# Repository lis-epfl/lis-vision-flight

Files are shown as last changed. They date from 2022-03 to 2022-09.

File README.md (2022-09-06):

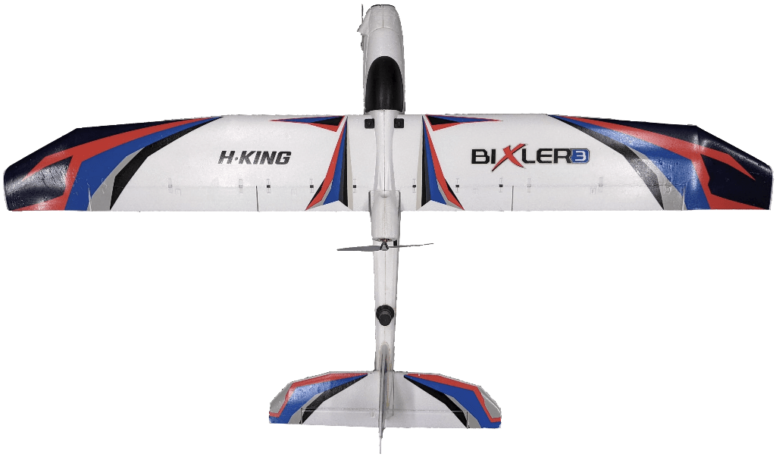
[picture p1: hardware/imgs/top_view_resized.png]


# LIS Vision Flight

Open source, simple fixed-wing drone for vision-based flight experiments

The LIS Vision flight project aims to give easy access to a vision-based fixed-wing drone to conduct experiments. It features

- a global shutter camera for vision-based applications
- an oboard single board computer to process vision data and for control
- a flow sensor and a point lidar for vision-based pose estimation
- a high precision RTK GNSS to provide ground truth data
- airspeed sensor for estimates of wind speeds
- a telemetry radio for communication with a ground station
- a PX4 autopilot that handles
  - sensor reading
  - actuator commanding
  - state estimation
  - time-synced camera triggering
  - attitude control
  - communication for RTK corrections

## Hardware

Instructions for building the drone can be found in [hardware](./hardware).

## Software

Find the instructions for the software setup in [software](./software).

## Citation

``` bibtex
@inproceedings{wueest2018accurate,
  title={Accurate Vision-based Flight with Fixed-Wing Drones},
  author={W{\"u}est, Valentin and Ajanic, Enrico and M{\"u}ller, Matthias and Floreano, Dario},
  booktitle={2022 IEEE/RSJ International Conference on Intelligent Robots and Systems (IROS)},
  year={2022},
  organization={IEEE}
}
```

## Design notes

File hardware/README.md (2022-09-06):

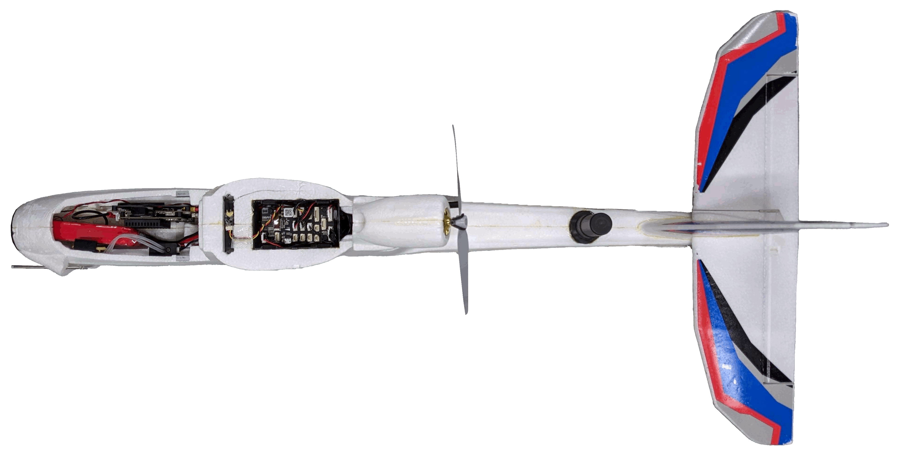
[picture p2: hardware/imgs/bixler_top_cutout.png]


# Hardware
## Parts list

We first provide a list of hardware components. The prices listed are based on online prices on March 11, 2022 and are listed in Euros.

### Body and actuation
| Part Function | Article Name | Amount | Price | Total Price |
| --- | --- | :----: | ----: | ---: |
| fixed-wing plane | H-King Bixler 3 Glider 1550mm (61") Kit | 1 | 100 | 100 |
| wing servos | Corona CS-929MG | 2 | 6 | 12 |
| elevator, rudder servo | Corona DS-919MG | 2 | 5 | 10 |
| thrust motor | Scorpion SII-2212-1400 KV (V2) | 1 | 42 | 42 |
| propeller | GWS EP-8040 | 1 | 5 | 5 |
| electronic speed controller (ESC) | Flycolor X-Cross Slim BL32 36A | 1 | 14 | 14 |
| battery | NVision LiPo 2400 mAh 3S 35C | 1 | 22 | 22 |
| power module | Micro Power Module (PM06 v2) | 1 | 15 | 15 |
| | | | | **220** |

### Autopilot 
| Part Function | Article Name | Amount | Price | Total Price |
| --- | --- | :----: | ----: | ---: |
| autopilot | Pixhawk 4 (plastic case) | 1 | 168 | 168 |
| RC receiver | FrSky R-XSR 2.4GHz 16CH ACCST | 1 | 21 | 21 |
| telemetry | Transceiver Telemetry Radio V3 500mW Telemetry Radio V3 433MHz | 1 | 51 | 51 |
| airspeed sensor | Sensirion SDP33 kit | 1 | 40 | 40 |
| GNSS antenna | Drotek DA233 | 1 | 70 | 70 |
| GNSS module | Drotek DP0601 | 1 | 170 | 170 |
| GNSS extension cable | 415-0031-MM250 | 1 | 15 | 15 |
| GNSS cable adapter | ADP-SMAM-SMAF90 | 1 | 6 | 6 |
| sd card autopilot | Sandisk Extreme microSDHC 16GB | 1 | 15 | 15 |
| | | | | **556** |

### Vision and companion computer
| Part Function | Article Name | Amount | Price | Total Price |
| --- | --- | :----: | ----: | ---: |
| camera | Flir Firefly S FFY-U3-16S2M-S | 1 | 190 | 190 |
| lens | Arducam 1/2.5" M12 6mm M2506ZH04 | 1 | 9 | 9 |
| single board computer (SBC) | Nvidia Jetson Nano | 1 | 121 | 121 |
| carrier board | Nvidia Jetson Nano Carrier Board | 1 | 100 | 100 |
| heatsink | ICK PGA 16 X 16 X 8 | 1 | 3 | 3 |
| usb wifi | TP-Link Archer T3U AC1300 Mini | 1 | 20 | 20 |
| sd card SBC | Sandisk Extreme microSDXC 64GB | 1 | 12 | 12 |
| | | | | **455** |

### Ground station

| Part Function  | Article Name | Amount | Price | Total Price |
| --- | --- | :----: | ----: | ---: |
| Laptop | - | 1 | - | - |
| Remote Control | FrSky Taranis X9D | 1 | 214 | 214 |
| Wifi Router | Ubiquity AmpliFi HD Mesh Router | 1 | 136 | 136 |
| Modem | Netgear LB2120 | 1 | 145 | 145 |
| GNSS antenna | Drotek DA233 | 1 | 70 | 70 |
| GNSS module | Drotek DP0601 | 1 | 170 | 170 |
| | | | | **735** |

### 3D printed parts
| Name | link | Image | Description |
| --- | --- | --- | --- |
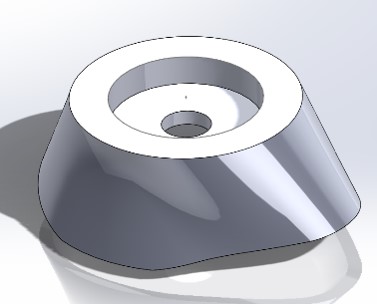
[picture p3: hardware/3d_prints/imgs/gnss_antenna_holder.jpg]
GNSS antenna holder
| GNSS antenna holder | [SLDPRT](3d_prints/gnss_antenna_holder.SLDPRT)<br />[STL](3d_prints/gnss_antenna_holder.STL)<br />[STEP](3d_prints/gnss_antenna_holder.STEP) |  | Attachment point for GNSS antenna. See step 2. |
| Pixhawk 4 foot (x2) | [SLDPRT](3d_prints/pixhawk_foot.SLDPRT)<br />[STL](3d_prints/pixhawk_foot.STL) | Pixhawk 4 foot | Tap M3 threads and attach to naked Pixhawk 4 board with nylon screws. See step 6 for instructions. |
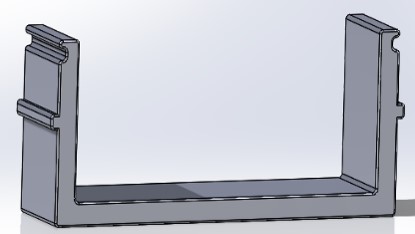
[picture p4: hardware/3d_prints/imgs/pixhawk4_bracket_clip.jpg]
Pixhawk 4 bracket clip
| Pixhawk 4 bracket clip (x2) | [SLDPRT](3d_prints/pixhawk_bracket_clip.SLDPRT)<br />[STL](3d_prints/pixhawk_bracket_clip.STL) |   | This part slides and clicks into place inside the "Pixhawk 4 bay". See step 6 for instructions. |
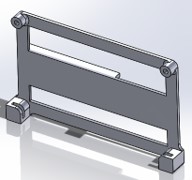
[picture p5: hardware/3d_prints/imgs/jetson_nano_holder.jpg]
Jetson nano holder
| Jetson nano holder | [SLDPRT](3d_prints/jetson_nano_holder.SLDPRT)<br />[STL](3d_prints/jetson_nano_holder.STL) |  | This part is glued with its back onto the right side of the front bay as shown in the picture of step 8. Two holes should be tapped with M3 thread to attach the LisNano board by its upper holes. Glue and test-fit the LisNano befor the assembly of the fuselage halves. |
| Airspeed sensor holder | [SLDPRT](3d_prints/airspeed_sensor_holder.SLDPRT)<br />[STL](3d_prints/airspeed_sensor_holder.STL) | Airspeed sensor holder | Tap M3 thread in the holes. Glue onto the shoulder on the left of the front bay as visible in the picture of step 8. |
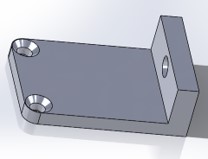
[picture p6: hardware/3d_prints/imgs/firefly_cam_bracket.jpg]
Firefly camera bracket
| Firefly camera bracket (x2) | [SLDPRT](3d_prints/firefly_camera_bracket.SLDPRT)<br />[STL](3d_prints/firefly_camera_bracket.STL) |  | Bracket to hold the Firefly camera in place. The two holes on the side allow screwing it onto the camera, the singular screw hole allow it to be inserted into the nose part and attached to it with an M3 nylon screw as shown in step 8. |
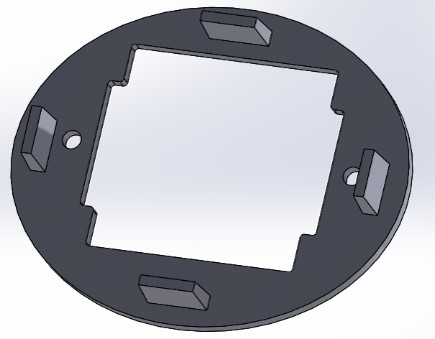
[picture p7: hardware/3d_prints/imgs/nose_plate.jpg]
Nose plate
| Nose plate | [SLDPRT](3d_prints/nose_plate.SLDPRT)<br />[STL](3d_prints/nose_plate.STL) |  | This part is glued to the front of the fuselage as visible in step 8. It accepts the front camera with brackets. Tap the holes with M3. |
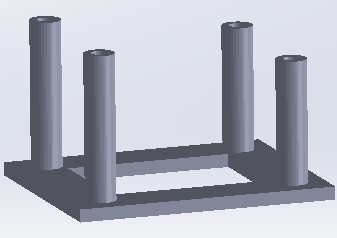
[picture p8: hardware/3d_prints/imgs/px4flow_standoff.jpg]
PX4Flow standoff
| PX4Flow standoff | [SLDPRT](3d_prints/px4flow_standoff.SLDPRT)<br />[STL](3d_prints/px4flow_standoff.STL) |  | This part is glued to the bottom inside the fuselage of the Bixler, see step 9. Make sure, the smaller standoffs are towards the back of the plane as they serve to level the flow sensor.  Tap M3 holes into the standoff. |
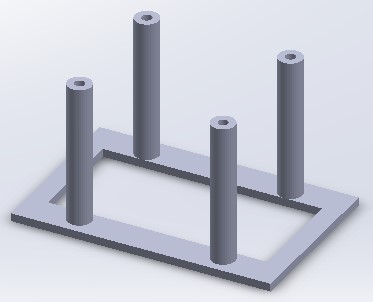
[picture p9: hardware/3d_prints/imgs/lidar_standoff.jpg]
PX4Flow standoff
| Lidar standoff | [SLDPRT](3d_prints/px4flow_standoff.SLDPRT)<br />[STL](3d_prints/lidar_standoff.STL) |  | The lidar standoff is placed inside the fuselage towards the front as shown in the figure in step 9. It is glued onto the fuselage with epoxy. Tap M3 holes into the standoff. |
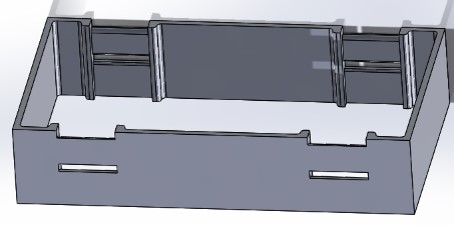
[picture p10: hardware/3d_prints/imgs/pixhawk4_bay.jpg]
Pixhawk 4 bay
| Pixhawk 4 bay | [SLDPRT](3d_prints/pixhawk_bay.SLDPRT)<br />[STL](3d_prints/pixhawk_bay.STL) |  | Is glued into the under-wing bay in step 10. The slot needs to be cut out slightly to fit. Make sure it's not deformed when inserted for glueing and that there is no epoxy in the slots and slits. |

### Tools

- M3 tap
- 5min epoxy
- servo tester

### Prepare body

We first give a short overview of most electornic parts that will be put inside the Bixler. Hopefully, this will serve as a guiding help.
*Note*: We use 5min epoxy to glue if not mentioned otherwise.

Bixler insides

**Step 1** Start printing all STL files which you find in the folder [3d_prints](3d_prints). Tap M3 threads into the 2 Pixhawk 4 feet, the Jetson nano holder, the airspeed sensor holder, the 2 Firefly camera brackets, the nose plate, the PX4Flow standoff and the lidar standoff.

**Step 2** Carve a groove into the tail of the Bixler to allow the antenna extension cable (SMA cable) to go from the tail to the fuselage as shown in the picture. Take the GNSS antenna holder and screw the male side of the SMA cable into it. This part (with SMA cable attached) is glued into the tail section of one of the fuselage parts (before fuselage halves are glued together). The SMA cable is glued into the groove cut in the fuselage half. The other end of the SMA cable should exit into the under-wing bay of the fuselage, high enough to allow screwing the GNSS module into the SMA connector, as shown in the picture.

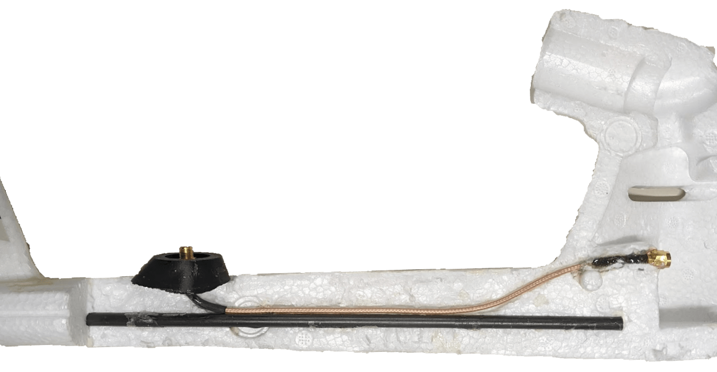
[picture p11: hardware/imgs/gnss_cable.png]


**Step 3** Set all servos to a zero position. You can do this with a servo tester or simply power it through the autopilot. Take the rudder/elevator-servos (2x Corona CS-929MG) and attach the arms at 90° angle such that they are facing outwards the fuselage. Connect the rods to the elevator and rudder in a hole in the servo arm at about 1.3cm distance and attach the arms to the servos. Now, glue the servos in place as shown in the picture.

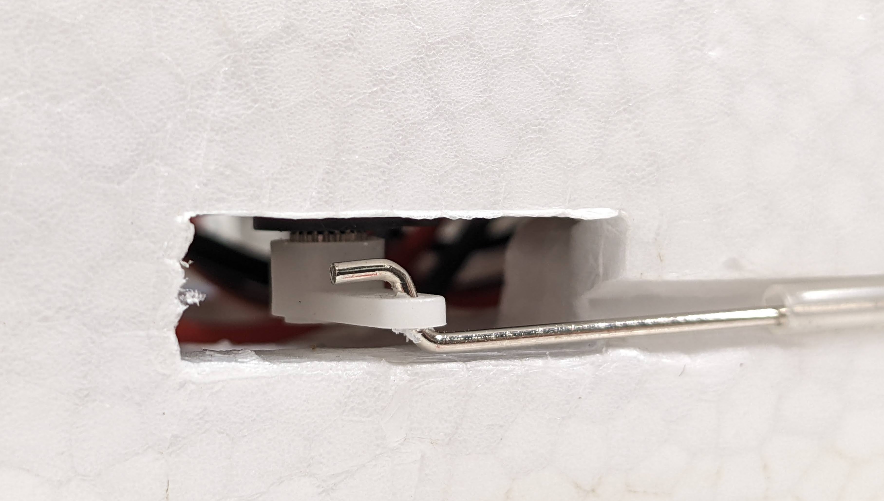
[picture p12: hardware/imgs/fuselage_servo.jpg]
outside
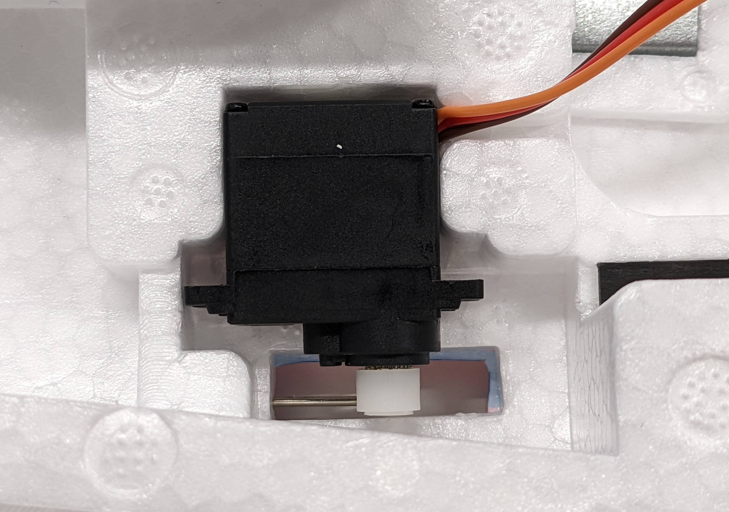
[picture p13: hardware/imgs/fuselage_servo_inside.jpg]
inside
    

**Step 4** Extend the wing servos cables. Then, attach the arms to the wing servos at a 90° angle and glue them in the wing. Attach the actuation rods as shown in the pic at a radius of about 1.1cm from the servo rotation center. For all actuation plastic parts, choose the second most outer hole. If you choose others, you will have to tune your controller accordingly afterwards. Then, glue in the plastic hinges on the ailerons and flaps. Finally, glue the flaps and the ailerons together by inserting a piece of foam as shown in the second picture and move ailerons and flaps to break them in.

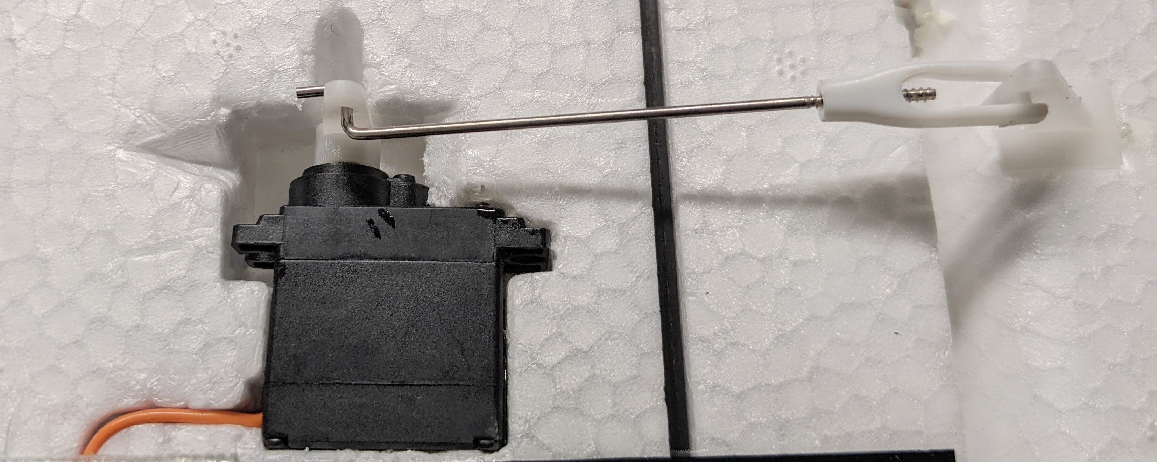
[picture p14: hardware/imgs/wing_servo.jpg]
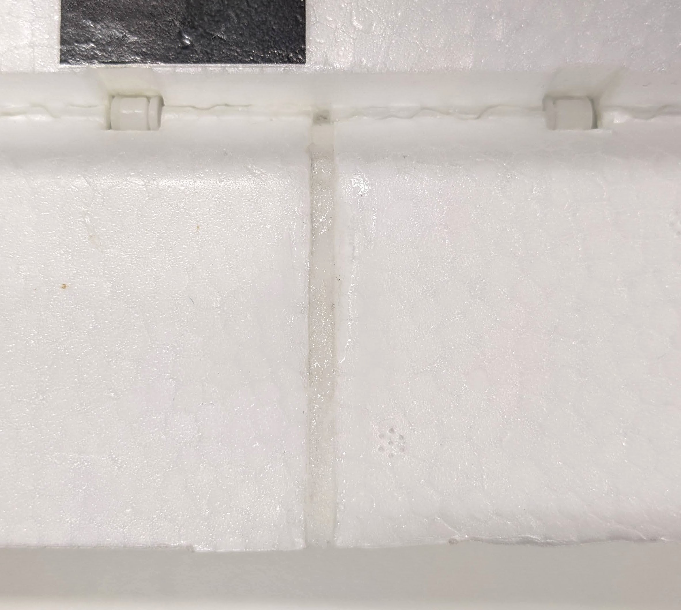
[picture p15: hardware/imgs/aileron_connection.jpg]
  

**Step 5** Glue horizontal and vertical tail wing together, cut off tail wheel, take off front wheels, take out plastic part to hold wheels in place in the center of the fuselage and the metal plate in the fuselage, as well. Glue the plastic motor mount into place, in the orientation as shown in the picture (make sure orientation is upward).

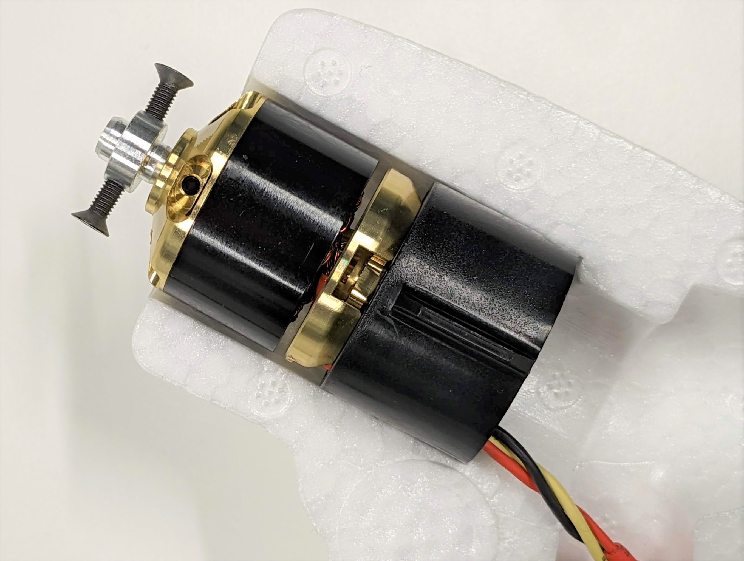
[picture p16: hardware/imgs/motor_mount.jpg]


**Step 6** Tap M3 threads and attach to naked Pixhawk 4 board with nylon screws. Attach the 2 Pixhawk 4 feet to the inside of the bracket using damping foam pads from Pixhawk 4 set.

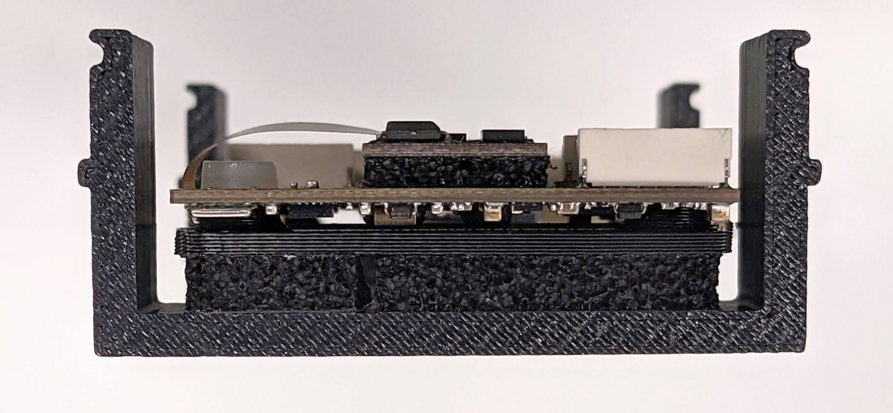
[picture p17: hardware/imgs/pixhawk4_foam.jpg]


**Step 7** Cut out all foam parts that obstruct inserts. Cut along the red lines as shown here. And glue the two halfs together.

inside

**Step 8** Screw the Firefly camera brackets onto the camera. Out of the foam parts that are meant for the wheels, cut a holder for the pitot tube as shown in the picture at (1). Glue on the pitot tube holder (1), the airspeed sensor holder (2), the nose plate (2), the Jetson nano holder (3) and the nose plate (4). Screw on the airspeed sensor, create a hole for the tubes to the pitot tube, add the camera and the Jetson nano.

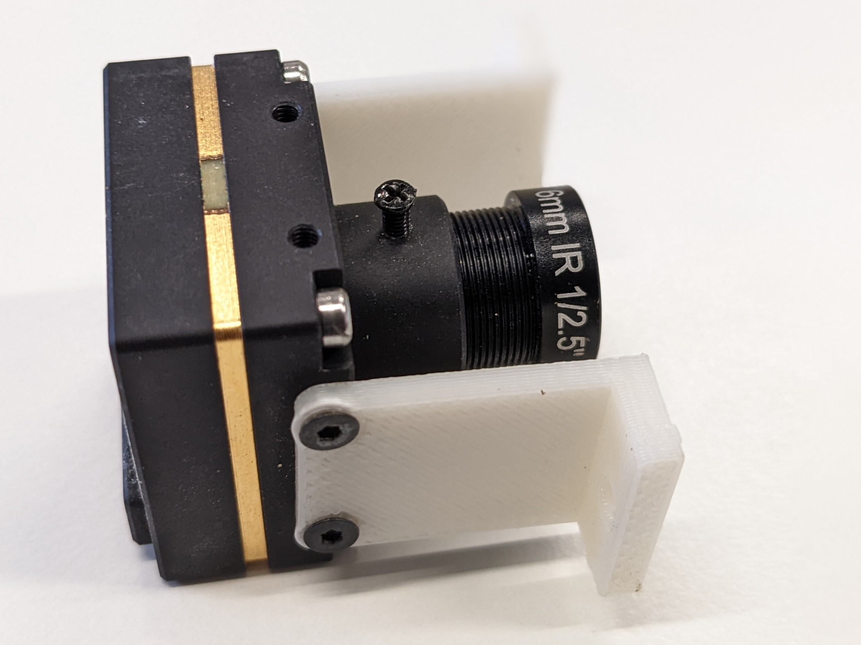
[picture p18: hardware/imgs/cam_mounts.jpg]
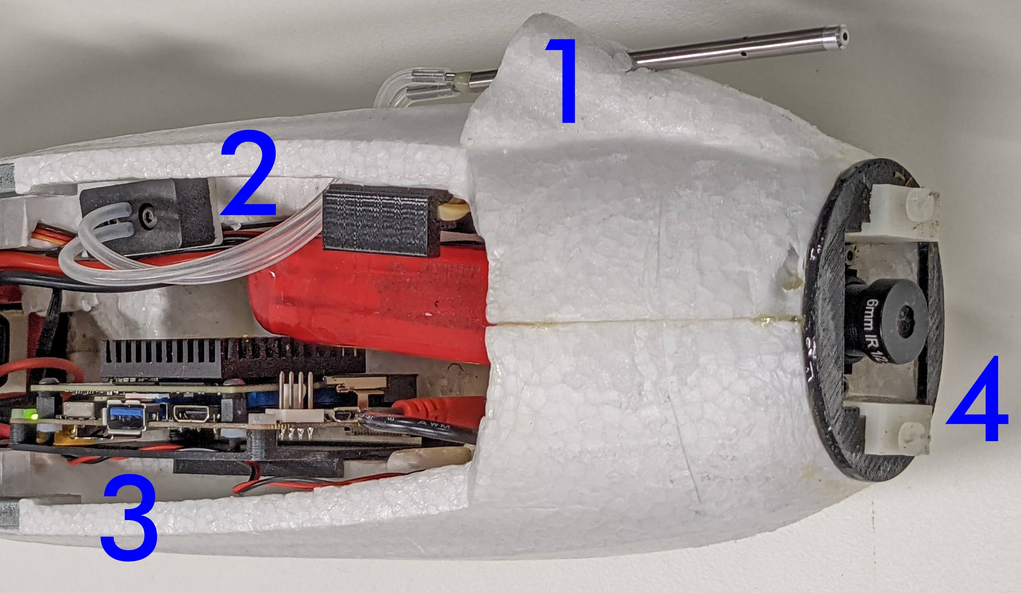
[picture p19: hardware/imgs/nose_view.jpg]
  

**Step 9** Glue the lidar standoff and the PX4Flow standoff to the base of the fuselage as shown in the image. Make sure there is enough space to allow to screw in the GNSS module. Screw on the GNSS module, the lidar and the PX4Flow.

inside

**Step 10** The Pixhawk 4 bay is glued into the under-wing bay (which needs to be cut out slightly to fit as shown in the first image). Make sure it's not deformed when inserted for glueing and that there is no epoxy in the slots and slits. The RC receiver sits in the slot next to it, where the wings are attached. Carve a lane in the foam along the Pixhawk 4 to lay down one of the antennas. Poke a hole on the side to guide out the other antenna and attach it with tape to the side as shown in the second image.

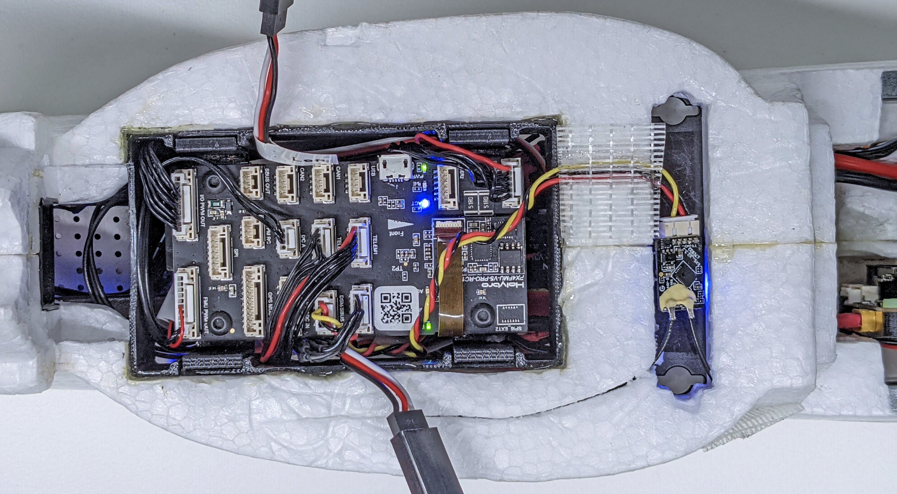
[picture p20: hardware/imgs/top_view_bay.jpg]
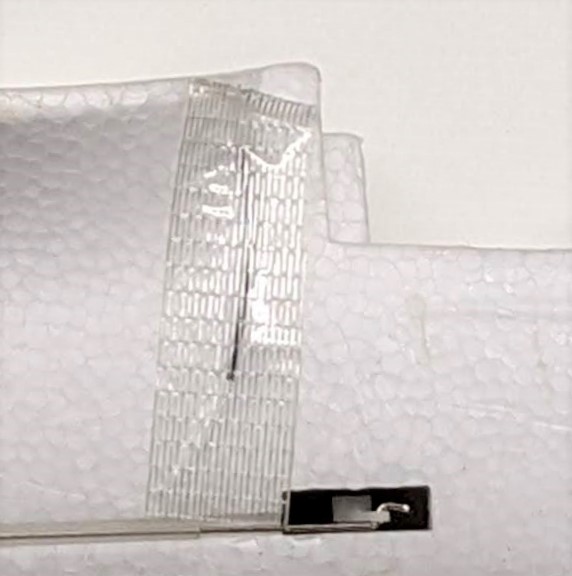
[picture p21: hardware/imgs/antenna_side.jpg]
  

**Step 11** Attach the Telemetry module with velcro tape to the inside of the Bixler, such that it will poke out through the air vent as shown in the image. Make sure it does not tuch the propeller. Finally, slide in the Pixhawk 4 into its bays until it clips into place.

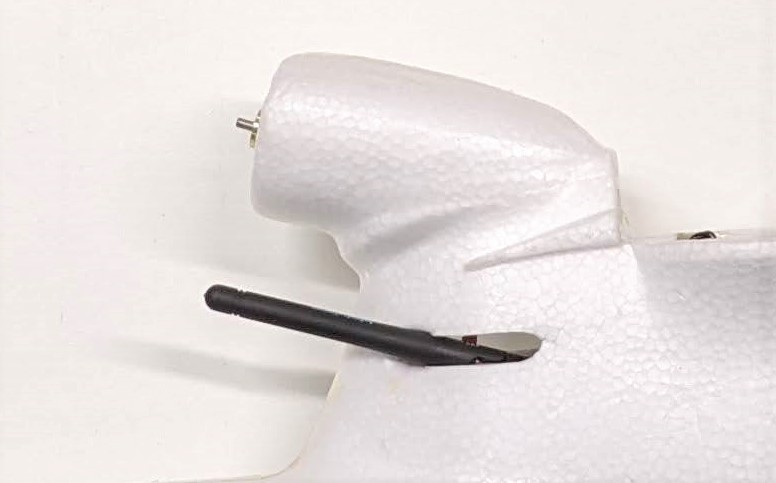
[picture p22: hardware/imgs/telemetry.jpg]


# Jetson Nano Carrier Board

If you decide to also use the Jetson Nano carrier board, we provide Altium files in the folder [carrier_board_nano](carrier_board_nano). Most useful is the folder [carrier_board_nano/Output](carrier_board_nano/Output), which contains all necessary files to get the PCB custom made. You can find a bill of materials, CAD files, Gerber files, Drill instruction files, assembly drawings and pick place files.

At a weight of 27g, the carrier board allows to power the board directly from a 2S to 4S LiPo battery. It features:
- USB 3.0 port
- mini HDMI port
- connector for a 5V fan
- micro USB port
- micro USB host port
- serial console port
- I2C connector
- UART connector
- MIPI CSI-2 camera connector
- SD card slot

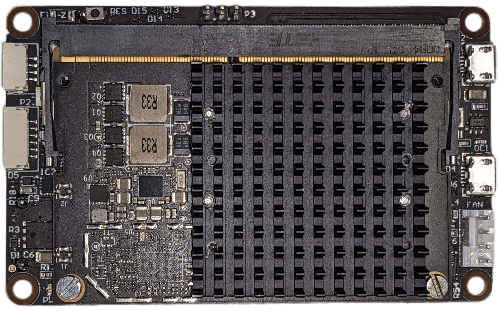
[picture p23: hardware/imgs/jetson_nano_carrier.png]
Jetson Nano with custom carrier board


Once you have the PCB custom made, we recommend replacing the large default heatsink on the jetson nano module with a smaller one, such as the ICK PGA 16 X 16 X 8 heatsink, by tapping holes into it from the bottom.

For instructions on setting up the software for the Jetson Nano, please refer to [../software](../software/)

# Wiring

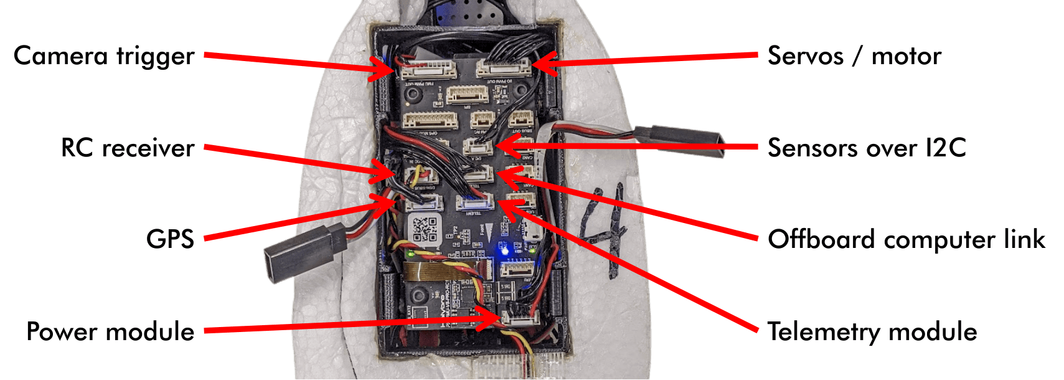
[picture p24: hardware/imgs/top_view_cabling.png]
Wiring overview

We show here a quick overview of the wiring and then go into more detail of each connection. For a detailed plan on the pinouts, please refer to [pinout guide](https://cdn.sparkfun.com/assets/e/9/4/6/8/Pixhawk4-Pinouts.pdf).

## Camera trigger

Connect the ground wire on the camera trigger to the ground on PX4 and the trigger wire to pin 5 or 6 on the `FMU PWM OUT`. For details on wiring and parameter settings, please refer to the official guide in [this section](https://docs.px4.io/v1.12/en/peripherals/camera.html). The trigger port on the camera can be defined in the [camera parameters file](../software/lis-vision-flight-ros/config/forward.yaml).

## RC receiver
Connect the RC receiver to the ports 1,2,5 on the DSM/SBUS connector as described on the [pinout guide](https://cdn.sparkfun.com/assets/e/9/4/6/8/Pixhawk4-Pinouts.pdf).

## Servos
Connect the connector board for the servos to the `I/O PWM OUT` port and connect the servos and the ESC of the thrust motor as described in the [Bormatec Maja airframe model](https://dev.px4.io/v1.10/en/airframes/airframe_reference.html#standard-plane).

| Channel | Actuator |
| --- | --- |
| MAIN1 | Aileron  |
| MAIN2 | Aileron  |
| MAIN3 | Elevator |
| MAIN4 | Throttle |
| MAIN5 | Rudder |

Do not connect the `VCC` voltage line to the servo distribution board, as these are powered by a power board, not by the Pixhawk 4 (see section **Power**).

## I2C sensors

Connect the I2C multiplex board to the `I2C A` connector on the Pixhawk 4 and the Px4Flow, the differential pressure sensor, and the point lidar to it. Please refer to the [PX4 lidar lite guide](https://docs.px4.io/v1.12/en/sensor/lidar_lite.html#wiring) for the wiring of the lidar module, as a capacitor needs to be connected to it. Do not connect the `VCC` voltage line to the I2C distribution board, as these are powered by a power board, not by the Pixhawk 4 (see section **Power**).

## Power

ATTTENTION, IMPORTANT

Follow these instructions, as the Pixhawk 4 is not meant to power servos and sensors. We power the servos and I2C sensor directly from the power board, so we do not use the power voltage coming from Pixhawk 4. 

To do so, connect the battery to the `GND` and `B+` connector on the power board. Then, connect the 6-pin connector with the pre-made cable to the Pixhawk 4 `POWER` port.

To avoid powering the I2C sensors and servos directly through the Pixhawk 4, we disconnect the `VCC` line on both the `FMU OUT` and the `I2C A` port from the connector.

To power the I2C sensor and servos through the power board directly, we connect the `5V` and `GND` port from the power module to one of the connectors on each of the breakout boards.

## Others

Use the pre-made cables for the following connections:
- connect the GPS `ROVER` connector to the `CAP & ADC IN` on the Pixhawk 4
- connect the telemtry module to `TELEM1` on the Pixhawk 4
- connect the UART connector on the Jetson Nano with the `TELEM2` port on the Pixhawk 4

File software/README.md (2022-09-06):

# Software

We provide instructions for the software setup. Here, we provide setting files for PX4 and the ROS files used for accurate vision based flight.

For instructions on how to setup a Jetson Nano with the custom carrier board, see [carrier_board_nano](./carrier_board_nano/).

## Install dependencies

First, install ROS melodic following the [official instructions](http://wiki.ros.org/melodic/Installation).

Then, clone the repository and update the submodule with
```bash
git clone https://github.com/lis-epfl/lis-vision-flight.git
cd lis-vision-flight
git submodule update --init --recursive
```

Install the ROS dependencies for Whycon and our package with these two commands
```bash
rosdep install -y --from-path software/whycon
rosdep install -y --from-path software/lis-vision-flight-ros
```

Build the whycon tag detector and source the catkin workspace

```bash
cd ../..
catkin_make
cd src/lis-vision-flight
source ../../devel/setup.bash
```

(Optional: We recommend creating a virtual environment for this step)

Get the python dependencies with

```bash
python2 -m pip install --user -r software/lis-vision-flight-ros/requirements.txt
```

## Prepare PX4

We use Firmware Version 1.10.1, which you can find [here](https://github.com/PX4/PX4-Autopilot/releases/tag/v1.10.1). You can load all parameter settings from the file [lis-vision-flight-ros/config/px4_parameters.params](lis-vision-flight-ros/config/px4_parameters.params) through QGroundControl (we use version 4.1.4, which you can find [here](https://github.com/mavlink/qgroundcontrol/releases/tag/v4.1.4)) or simply inspect them and adjust the values as you see fit. Please refer to the [PX4 parameter list](https://docs.px4.io/v1.10/en/advanced_config/parameter_reference.html) for more information on each of the parameters.

On the SD card in the PX4 Autopilot, edit (or create if it doesn't exit) the file `/etc/extras.txt` and add these lines
```
ekf2 stop
gps stop
gps start
px4flow stop
ll40ls stop
ll40ls start -b 4
sleep 8
px4flow start -a 0x45
ekf2 start

mavlink stream -d /dev/ttyS2 -r 100 -s ATTITUDE_QUATERNION
mavlink stream -d /dev/ttyS2 -r 50  -s LOCAL_POSITION_NED
mavlink stream -d /dev/ttyS2 -r 50  -s WIND_COV
mavlink stream -d /dev/ttyS2 -r 50  -s VFR_HUD
mavlink stream -d /dev/ttyS2 -r 50  -s ACTUATOR_CONTROL_TARGET0
mavlink stream -d /dev/ttyS2 -r 100 -s HIGHRES_IMU
mavlink stream -d /dev/ttyS2 -r 100 -s ATTITUDE
mavlink stream -d /dev/ttyS2 -r 50  -s NAV_CONTROLLER_OUTPUT
mavlink stream -d /dev/ttyS2 -r 50  -s GLOBAL_POSITION_INT
mavlink stream -d /dev/ttyS2 -r 50  -s GLOBAL_POSITION_SETPOINT_INT
mavlink stream -d /dev/ttyS2 -r 50  -s GPS_RAW_INT
mavlink stream -d /dev/ttyS2 -r 50  -s POSITION_TARGET_GLOBAL_INT
mavlink stream -d /dev/ttyS2 -r 50  -s SERVO_OUTPUT_RAW
mavlink stream -d /dev/ttyS2 -r 20  -s DISTANCE_SENSOR
```
This will set the right ports for the sensors and will set the required streaming rates.

## Flir camera

If you are using the Flir camera, we recommend using the [flir_camera_driver](https://github.com/ros-drivers/flir_camera_driver) for ROS. Make sure you first install the Spinnaker SDK, which you can get from the [Spinnaker SDK download page](https://www.flir.eu/support-center/iis/machine-vision/downloads/spinnaker-sdk-and-firmware-download/).

We recommend calibrating the camera with [Kalibr](https://github.com/ethz-asl/kalibr). This will help you to get the right camera parameters, which you can put in the [calibration config file](lis-vision-flight-ros/config/19308195.yaml).

We provide a launch file that allows triggering the camera from PX4 in [flir_camera.launch](lis-vision-flight-ros/launch/flir_camera.launch).

## Run

To run the controller as we did in the publication, you can then launch the camera ([camera launch file](lis-vision-flight-ros/launch/flir_camera.launch)), the connection of the Jetson nano to the PX4 Autopilot with mavros and the vision based controller ([controller launch file](lis-vision-flight-ros/launch/vision_gnss_controller.launch)) with

``` bash
roslaunch lis-vision-flight run.launch
```

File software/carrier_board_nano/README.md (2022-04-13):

# Software

We first describe how to set up the custom Jetson Nano carrier board. All of the instructions were tested on a host system with Ubuntu 18.04 LTS.

1. Install Nvidia SDK Manager which you can find here: https://docs.nvidia.com/sdk-manager/download-run-sdkm/index.html

1. Run the SDK Manager, choose Jetson Nano as Target Hardware and JetPack 4.4 as Target OS. Click next and select P3448-000 Jetson Nano [developer kit version] and continue with download and install. For now, skip the flashing of the Nano when prompted. JetPack will be installed on `~/nvidia/nvidia_sdk/JetPack_4.4_Linux_JETSON_NANO_DEVKIT/Linux_for_Tegra/`.

1. Create the folder `~/nvidia/nvidia_sdk/JetPack_4.4_Linux_JETSON_NANO_DEVKIT/Linux_for_Tegra/sources` and extract the [kernel sources](https://developer.nvidia.com/embedded/dlc/r32-3-1_Release_v1.0/Sources/T210/public_sources.tbz2) into it. Make sure to also extract all the containers inside the file you download.

1. Download and unpack [dts.zip](./carrier_board_nano/dts.zip) on your host machine. Copy the `tegra210-p3448-0002-p3449-0000-b00.dts` and `tegra210-porg-p3448-common.dtsi` to `~/nvidia/nvidia_sdk/JetPack_4.4_Linux_JETSON_NANO_DEVKIT/Linux_for_Tegra/sources/hardware/nvidia/platform/t210/porg/kernel-dts/`  folder (overwrite). Copy the two `...lis_nano...` files to `./porg-platforms` subfolder.

1. Download and extract the [Linaro GCC](http://releases.linaro.org/components/toolchain/binaries/7.3-2018.05/aarch64-linux-gnu/gcc-linaro-7.3.1-2018.05-x86_64_aarch64-linux-gnu.tar.xz) to `~/opt/`.

1. Copy these 3 lines at the end of `~/.bashrc`:
    
    ``` bash
    export CROSS_COMPILE=$HOME/opt/gcc-linaro-7.3.1-2018.05-x86_64_aarch64-linux-gnu/bin/aarch64-linux-gnu-
    export LOCALVERSION=-tegra
    export TEGRA_KERNEL_OUT=$HOME/nvidia/kernel_img
    ```
    and then run `source ~/.bashrc`.

1.  Navigate to `~/nvidia/nvidia_sdk/JetPack_4.4_Linux_JETSON_NANO_DEVKIT/Linux_for_Tegra/sources/kernel/kernel-4.9` and run:
    ``` bash
    mkdir -p $TEGRA_KERNEL_OUT
    make ARCH=arm64 O=$TEGRA_KERNEL_OUT tegra_defconfig
    make ARCH=arm64 O=$TEGRA_KERNEL_OUT dtbs
    cp ~/nvidia/kernel_img/arch/arm64/boot/dts/tegra210-p3448-0002-p3449-0000-b00.dtb ~/nvidia/nvidia_sdk/JetPack_4.4_Linux_JETSON_NANO/Linux_for_Tegra/kernel/dtb/
    ```

1. Copy the script [l4t_create_default_user.sh](carrier_board_nano/l4t_create_default_user.sh) to `~/nvidia/nvidia_sdk/JetPack_4.4_Linux_JETSON_NANO_DEVKIT/Linux_for_Tegra/` and move to the folder in a shell. Run
    ``` bash
    sudo ./l4t_create_default_user.sh -u lis -p lislis
    ```
    replace `lis` and `lislis` with your username and password.

1. Put the board into the ForcedRecovery mode (press "RECOV" button and while holding it, reset with "RES" button). Plug a standard micro-USB cable into the Ethernet over USB port (see image below). Check that an "Nvidia" device is showing up after issuing of `lsusb` command.

1. Flash the Nano module with `sudo ./flash.sh jetson-nano-emmc mmcblk0p1` to flash it on the emmc or `./flash.sh jetson-nano-qspi-sd mmcblk0p1` to flash it to the SD card.

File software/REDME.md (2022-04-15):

# Software

We provide instructions for the software setup. First, we describe the software infrastructure, provide setting files for PX4, and provide the controller file used for the accurate vision based flight.

For instructions on how to setup a Jetson Nano with the custom carrier board, see [carrier_board_nano](./carrier_board_nano/).

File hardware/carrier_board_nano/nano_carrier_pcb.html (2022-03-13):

Altium customize

# Board Information Report

Date: | | 15/10/2020
Time: | | 10:52:36
Elapsed Time: | | 00:00:01
Filename: | | D:\projects\nano-carrier\Altium\V_1_1\nano_carrier_pcb.PcbDoc
Units: | | mmmils

## Contents

Contents

Board Specification

General

Copper Area

Copper Area

Board Holes

Plated Hole Size

Board Slots

Plated Slot Size

Other

Track Width

## Board Specification

General
Board Size | 88mm x 54mm
Components on board | 168

Back to top

## Copper Area

Layer | Sq.In. | Sq.MM. | Percent of layer
Top Layer | 1,822 | 1175,558 | 25%
GND | 6,713 | 4331,218 | 91%
PWR | 6,507 | 4197,97 | 88%
Bottom Layer | 0,549 | 354,021 | 7%
Total | NaN | NaN

Back to top

## Board Holes

Plated Hole Size | Pads | Vias
0mm | 712 | 0
0.2mm | 0 | 270
0.3mm | 0 | 115
0.7mm | 9 | 0
0.9mm | 11 | 0
1.05mm | 4 | 0
1.1mm | 2 | 0
1.8mm | 2 | 0
Total | 740 | 385

Back to top

## Board Slots

Plated Slot Size / Length | Pads
19.685mil / 47.244mil | 4
23.622mil / 43.307mil | 2
23.622mil / 51.181mil | 2
23.622mil / 59.055mil | 2
23.622mil / 90.551mil | 2
Total | 12

Back to top

## Other

Track Width | Count
0.0254mm | 220
0.05mm | 30
0.08mm | 2
0.1mm | 1073
0.127mm | 593
0.1431mm | 145
0.15mm | 1022
0.1618mm | 282
0.17mm | 8
0.1796mm | 118
0.2mm | 106
0.25mm | 150
0.254mm | 106
0.3mm | 18
0.381mm | 75
0.4mm | 302
0.5mm | 114
0.6mm | 5
1mm | 4
Total | 4373

Back to top

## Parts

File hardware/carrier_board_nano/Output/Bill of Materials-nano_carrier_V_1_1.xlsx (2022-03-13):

Designator | Supplier 1 | Supplier Part Number 1 | Quantity | Value | Footprint | Description | Comment
D5 | Digi-Key | 1N4148WSFSCT-ND | 1 | 1N4148WS | SOD-323 | Diode small signal | 1N4148WS
CR1225 | Digi-Key | 36-3000CT-ND | 1 |  | CR1225_Holder | Header, 2-Pin | Header 2
U8 | Digi-Key | 296-16844-1-ND | 1 |  | SC70-6 | 1.8 - 5.5V fast level translator | SN74LVC1T45
U3 | Digi-Key | 296-21929-1-ND | 1 |  | PW0014A_L | Bidir. voltage level translator | TXB0104PWR
U5 | Digi-Key | 296-25269-1-ND | 1 | TLV70018DCKT | SC70-5 | Voltage Regulator, 2V to 5.5V, 175mV Dropout, 1.8Vout, 200mAout | TLV70018DCKT
D2, D3, D4, D6, D8, D9, D10, D12, D13, D14, D15, D17 | Digi-Key | 296-25410-1-ND | 12 | TPD2E009DRTR | SOT-3 | ESD Suppressors 2-CH | TPD2E009DRTR
U2 | Digi-Key | 296-32603-1-ND | 1 |  | TSOP8_065pitch | Bidirectional voltage level translator | TXS0102DCU
U6 | Digi-Key | 296-35972-1-ND | 1 |  | FP-DGK0008A-MFG | IC TRNSLTR BIDIRECTIONAL 8VSSOP | TCA9517DGKR
E2, E3 | Digi-Key | 296-43875-1-ND | 2 |  | TPD4E02B04 |  | TPD4E02B04
R11, R15 | Digi-Key | 311-0.0GRCT-ND | 2 | 0 | res0603 | 100K | 0603 1%
R20, R50 | Digi-Key | 311-1.00KHRCT-ND | 2 | 1K | res0603 | 100K | 0603 1%
R19 | Digi-Key | 311-100KHRCT-ND | 1 | 100K | res0603 | 100K | 0603 1%
R21, R51, R56 | Digi-Key | 311-150HRCT-ND | 3 | 150R | res0603 | 100K | 0603 1%
R12 | Digi-Key | 311-330HRCT-ND | 1 | 330R | res0603 |  | 0603 1%
C7, C11, C34 | Digi-Key | 399-5620-1-ND | 3 | 100u | cap1206 |  | 1206 6.3V
C6 | Digi-Key | 445-8045-1-ND | 1 | 22u | cap1206 |  | 1206 35V
C10 | Digi-Key | 445-9066-1-ND | 1 | 1u | 0402 | MLCC SMT Capacitor 1uF 0402 | 1u
I2C | Digi-Key | 455-1566-1-ND | 1 |  | JST_GH_4_side | Header, 4-Pin | SM04B-GHS-TB
UART | Digi-Key | 455-1568-1-ND | 1 |  | JST_GH_6_side | Header, 6-Pin | SM06B-GHS-TB
OC1, OC2 | Digi-Key | 475-2506-1-ND | 2 |  | led_0603 | standard LED | diode_LED
PWR | Digi-Key | 475-2709-1-ND | 1 |  | led_0603 | Green LED 0603 | green LED
L1, L3, L4 | Digi-Key | 490-3992-1-ND | 3 | BLM18EG221SN1D | fb0603 | MURATA BLM18EG221SN1D FERRITE BEAD, 0.05OHM, 2A, 0603 | BLM18EG221SN1D
C18 | Digi-Key | 490-6051-1-ND | 1 | 0.1uF | CAP0603 | Ceramic capacitor, SMD, 0603, 25V, 10%, X7R | .Value
C8 | Digi-Key | 490-6335-1-ND | 1 | 47n | cap0402 |  | 0402 6.3V
C9, C19, C20, C21, C36, C37, C39, C40, C41 | Digi-Key | 490-10474-1-ND | 9 | 10uF | cap0603 | standard, non-polarized capacitor | 0603 10V
C4, C5, C14, C15, C16, C17, C22, C23, C24, C25, C26, C27, C28, C29, C30, C31, C32, C33, C35, C38 | Digi-Key | 490-14603-1-ND | 20 | 0.1u, 0.1uF | cap0402, cap0402_void | [NoValue], standard, non-polarized capacitor | 0402 6.3V, 0402
IC1, IC3, IC4 | Digi-Key | 576-1680-1-ND | 3 | MIC2009 | TSOP-6 | POWER LOAD SWITCH, HIGH SIDE | MIC2009
L2 | Digi-Key | 587-3605-1-ND | 1 | 4.7uH | NRS5030 | Inductor | Inductor
C1, C2, C3 | Digi-Key | 587-4280-1-ND | 3 | 47u | cap0805 |  | 0805 6.3V
J2, J4 | Digi-Key | 609-4616-1-ND | 2 |  | micro_usb_TH_RA_10118193 | CONN USB MICRO B RECPT SMT+TH R/A | 10118193-0001LF
J5 | Digi-Key | 732-2739-1-ND | 1 |  | mini_HDMI_WE_685119136923 |  | HDMI_C
J1 | Digi-Key | 732-3147-1-ND | 1 |  | 692121230100 | USB 3.0 Type A, Receptacle, Horizontal, THR, with Offset 1.04mm | USB 3.0 Type A Receptacle
SP1, SP2 | Digi-Key | 732-12984-ND | 2 | 9774060151 | M2.5-6mm | M2.5-6mm | 9774060151
DCDC1 | Digi-Key | 1589-2043-ND | 1 |  | MPM3550E |  | MPM3550
Q2, Q3, Q4, Q5, Q6, Q7 | Digi-Key | 1727-1280-1-ND | 6 | NX3008NBKW | SC70-3 | MOSFET, N CH, 60V, 0.2A | NX3008NBKW
D7, D18 | Digi-Key | 1727-1338-1-ND | 2 |  | DFN1608D-2 | Schottky diode | diode_schottky
IC2 | Digi-Key | 1727-3213-1-ND | 1 | 74HC00BQ | DHVQFN14 | 2 NAND Gate, 4 channel | 74HC00BQ
M1 | Digi-Key | A126764CT-ND | 1 | 2309413-1 | jetson-nano-connector | Memory Socket, DDR4, SODIMM Socket, 260 Contacts, Copper Alloy, Gold Plated Contacts | 2309413-1
D11 | Digi-Key | BAS70W-05FDICT-ND | 1 | BAS70W | SC70 | BAT54S schottky protection | .Value
F1 | Digi-Key | F5787CT-ND | 1 | 1206L450SLWR | res1206 | PTC RESET 6V LO RHO 1206 4.50A | 1206L450SLWR
Q1 | Digi-Key | FDWS9508L-F085OSCT-ND | 1 |  | DFN8_5x6 | P-Channel MOSFET in DFN8 package (DFN5) | MOSFET-P
D1 | Digi-Key | MMSZ5240BS-FDICT-ND | 1 |  | sod323 | Zener diode | diode_zener
R13, R14 | Digi-Key | P1.00KLCT-ND | 2 | 1K | res0402 | 100K | 0402 1%
R43, R44 | Digi-Key | P2.00KLCT-ND | 2 | 2K | res0402 | 100K | 0402 1%
R41, R42, R45 | Digi-Key | P10.0KLCT-ND | 3 | 10K | res0402 | 100K | 0402 1%
R1, R3, R10, R22, R40, R53, R55 | Digi-Key | P14.3KLCT-ND | 7 | 14K3 | res0402 |  | 0402 1%
R49 | Digi-Key | P33.0KLCT-ND | 1 | 33K | res0402 | 100K | 0402 1%
R2, R4, R7, R8, R47, R48, R54 | Digi-Key | P100KLCT-ND | 7 | 100K, 200K | res0402 | 100K | 0402 1%
R46 | Digi-Key | P162KLCT-ND | 1 | 162K | res0402 | 100K | 0402 1%
R16, R17, R52 | Digi-Key | P200KLCT-ND | 3 | 200K | res0402 | 100K | 0402 1%
R18 | Digi-Key | P470KLCT-ND | 1 | 470K | res0402 | 100K | 0402 1%
R32, R33, R34, R35, R36, R37, R38, R39 | Digi-Key | P499LCT-ND | 8 | 499R | res0402_void |  | 0402 1%
R24, R25, R26, R27, R28, R29, R30, R31 | Digi-Key | RMCF0402FT5R60CT-ND | 8 | 5R6 | res0402_void |  | 0402 1%
RECOV., RES | Digi-Key | SW1020CT-ND | 2 |  | b3u_1000p | Single-Pole, Single-Throw Switch | Reset
U4 | Digi-Key | TS30042-M033QFNRCT-ND | 1 |  | qfn16_TP | 40V,2A synch voltage reg, QFN16 3x3mm | TS30042
FAN | Digi-Key | WM4330-ND | 1 |  | 47053-1000 | Fan header, 4-Pin | 0470531000
SD1 | Digi-Key | WM6357CT-ND | 1 |  | uSD_MOLEX_1040310811 |  | uSD_MOLEX_1040310811
CAM | Digi-Key | WM10967CT-ND | 1 |  | molex_52271_15pin | 15 pin FPC connector | mipi_csi_15pin

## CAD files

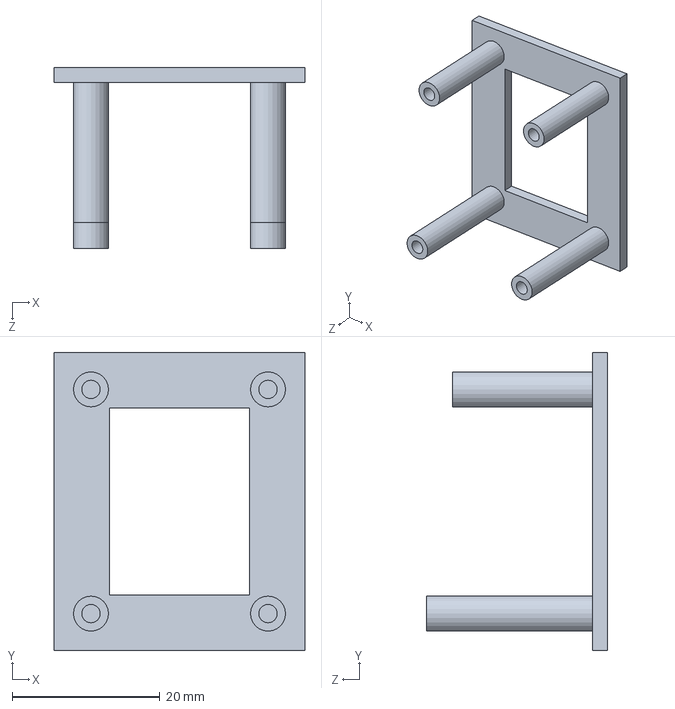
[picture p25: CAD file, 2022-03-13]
hardware/3d_prints/px4flow_standoff.SLDPRT
34.0 x 40.4 x 24.5 mm

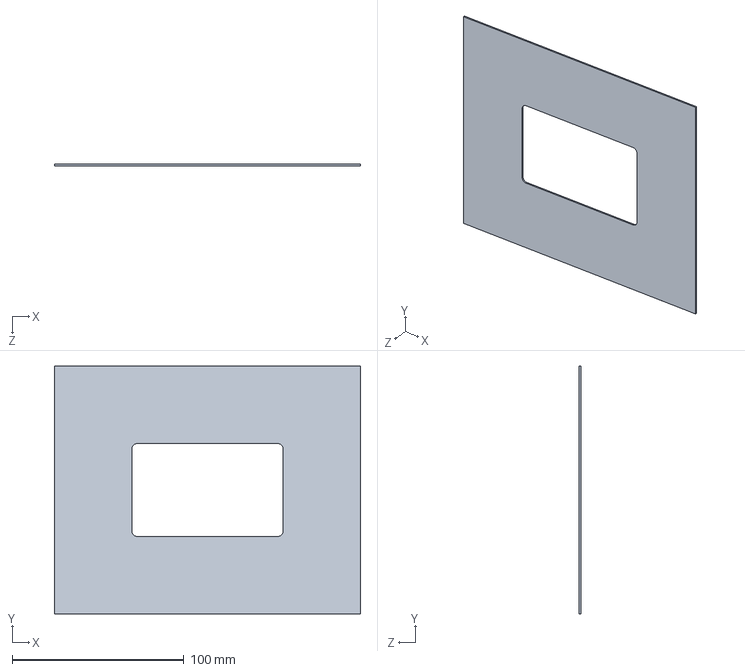
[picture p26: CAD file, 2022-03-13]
hardware/carrier_board_nano/CAD/pcb_frame.SLDPRT
178.0 x 144.0 x 1.00 mm

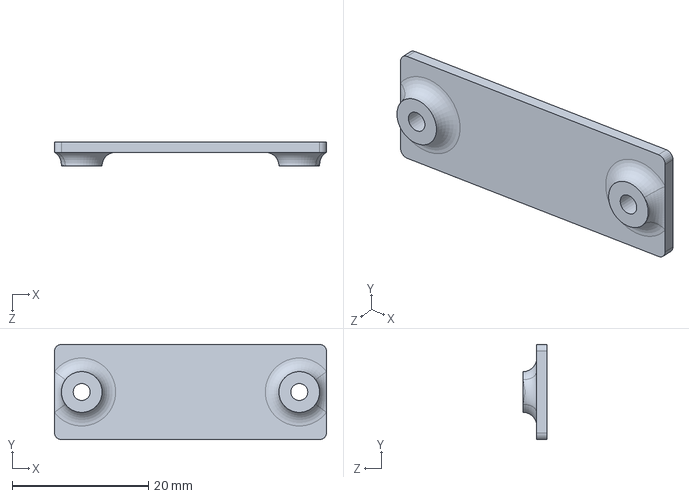
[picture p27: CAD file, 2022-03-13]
hardware/3d_prints/pixhawk_foot.SLDPRT
40.0 x 14.0 x 3.50 mm

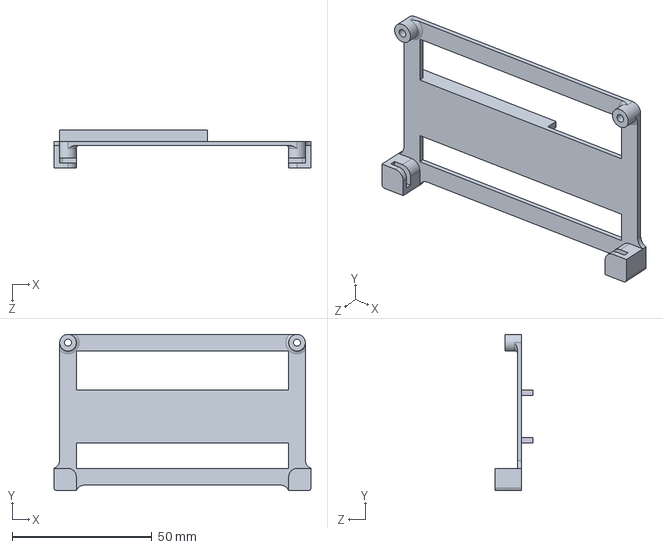
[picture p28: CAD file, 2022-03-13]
hardware/3d_prints/jetson_nano_holder.SLDPRT
92.0 x 56.0 x 13.5 mm

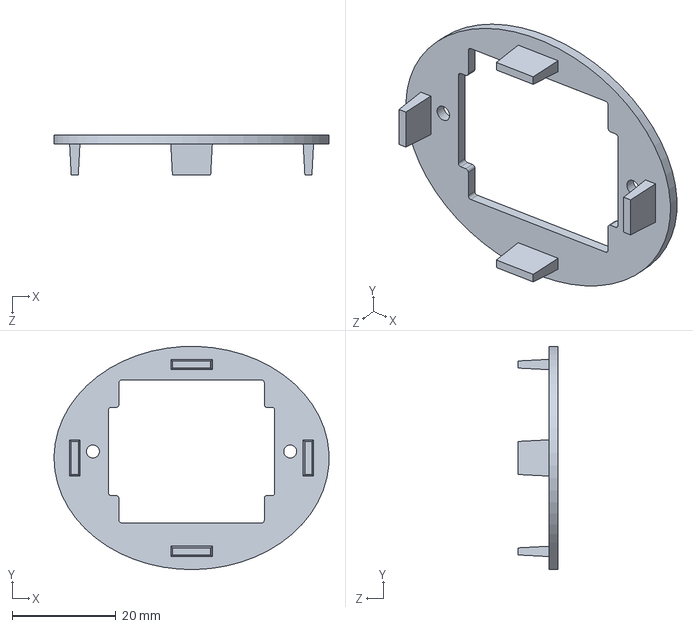
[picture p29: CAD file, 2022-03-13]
hardware/3d_prints/nose_plate.SLDPRT
53.0 x 43.0 x 7.70 mm

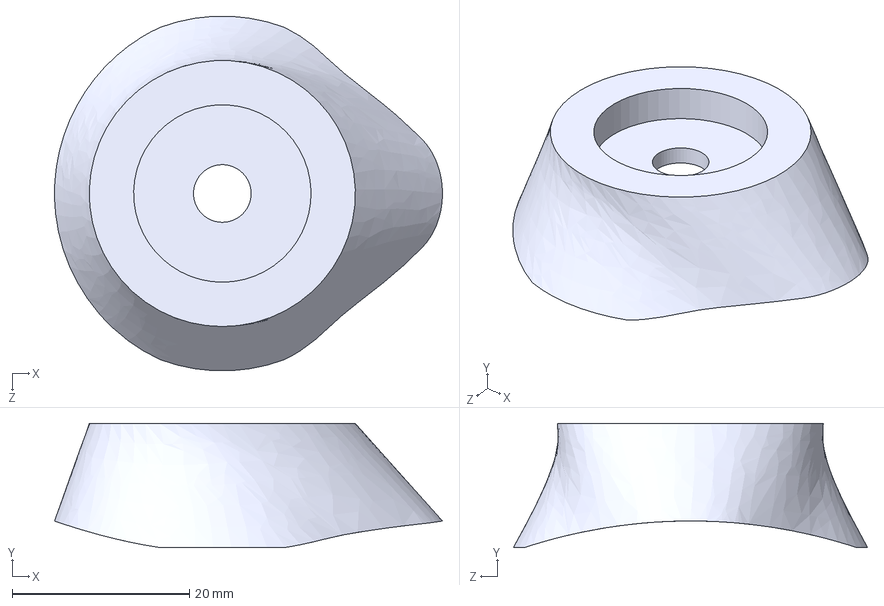
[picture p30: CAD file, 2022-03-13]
hardware/3d_prints/gnss_antenna_holder.STEP
43.7 x 14.0 x 39.9 mm

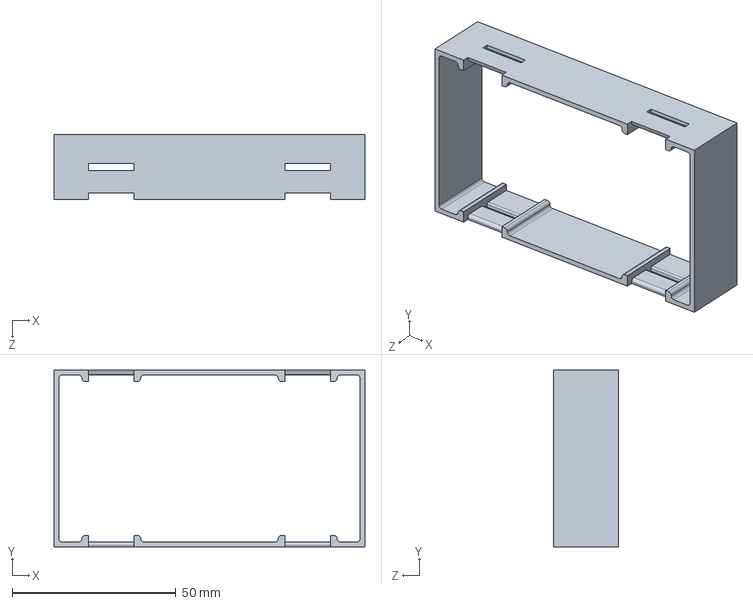
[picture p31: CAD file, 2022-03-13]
hardware/3d_prints/pixhawk_bay.SLDPRT
95.0 x 54.0 x 20.0 mm

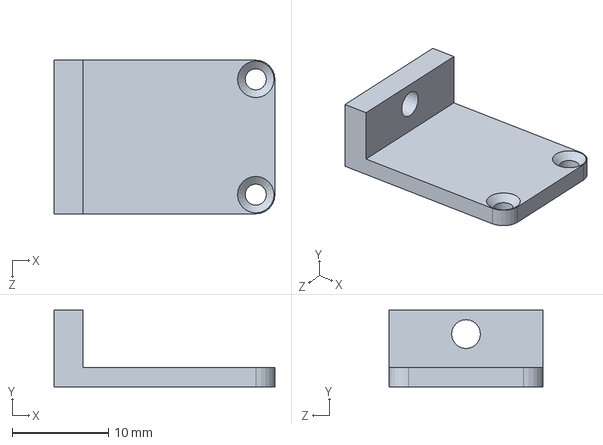
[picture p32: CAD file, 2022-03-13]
hardware/3d_prints/firefly_camera_bracket.SLDPRT
23.0 x 8.00 x 16.0 mm

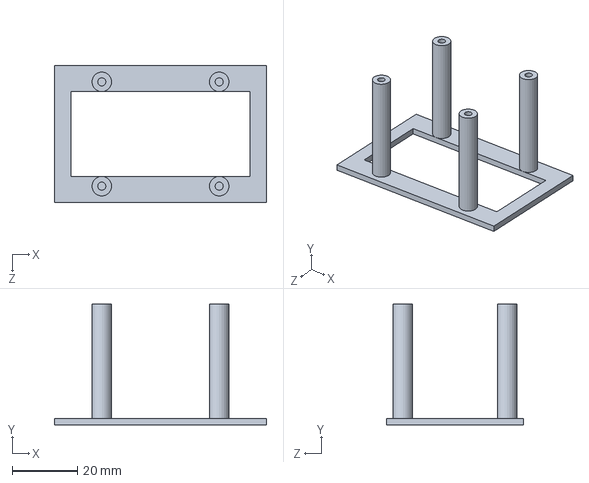
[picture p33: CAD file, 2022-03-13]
hardware/3d_prints/lidar_standoff.SLDPRT
65.0 x 37.0 x 42.0 mm

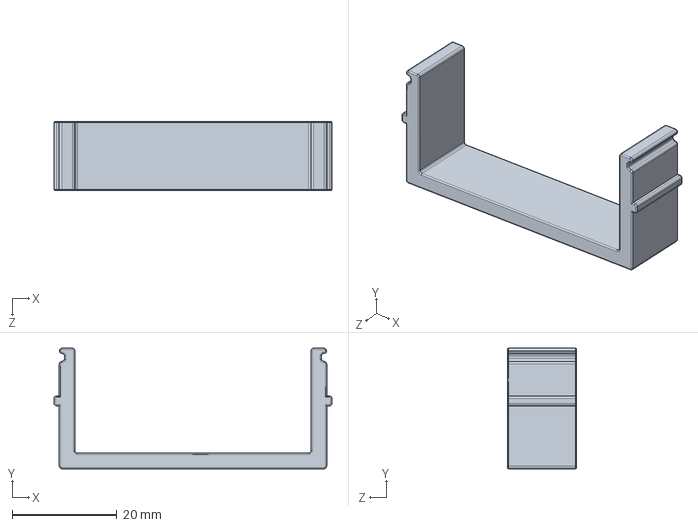
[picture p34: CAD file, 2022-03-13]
hardware/3d_prints/pixhawk_bracket_clip.SLDPRT
53.0 x 23.0 x 13.2 mm

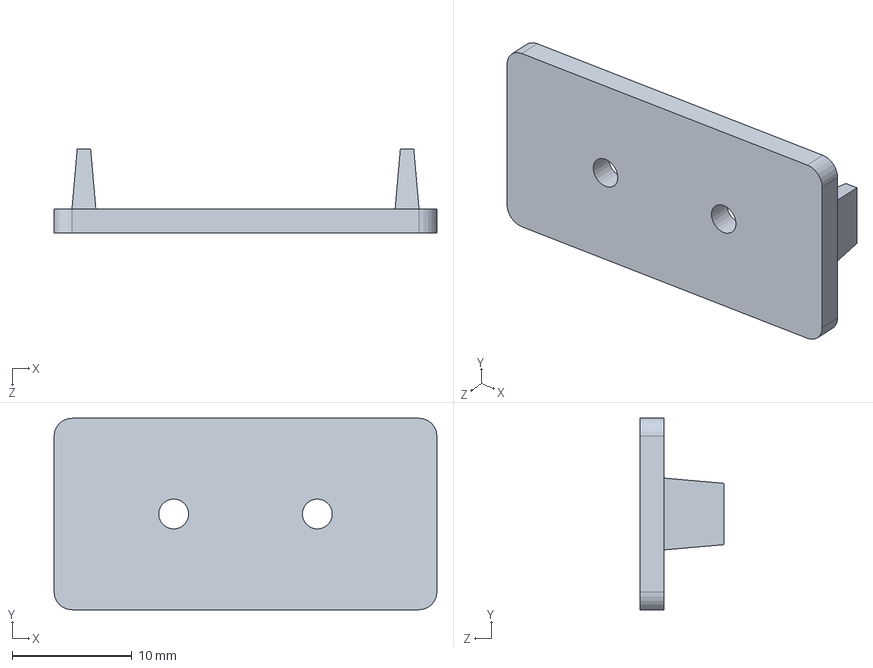
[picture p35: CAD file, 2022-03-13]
hardware/3d_prints/airspeed_sensor_holder.SLDPRT
32.0 x 16.0 x 7.00 mm

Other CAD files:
hardware/3d_prints/airspeed_sensor_holder.STL
hardware/3d_prints/firefly_camera_bracket.STL
hardware/3d_prints/gnss_antenna_holder.SLDPRT
hardware/3d_prints/gnss_antenna_holder.STL
hardware/3d_prints/jetson_nano_holder.STL
hardware/3d_prints/lidar_standoff.STL
hardware/3d_prints/nose_plate.STL
hardware/3d_prints/pixhawk_bay.STL
hardware/3d_prints/pixhawk_bracket_clip.STL
hardware/3d_prints/pixhawk_foot.STL
hardware/3d_prints/px4flow_standoff.STL

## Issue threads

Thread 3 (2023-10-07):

Will this code run on Jackal robot?

zhang-mu-zhi, 2023-10-07:
这个代码可以在Jackal robot上运行吗？
我没有固翼无人机，但是我有一个Jackal robot，我想将这个代码用在Jackal robot请问可以吗？
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

zhang-mu-zhi, 2023-10-07:
> 这个代码可以在 Jackal 机器人上运行吗？ 我没有固翼无人机，但是我有一个 Jackal 机器人，我想将这个代码用在 Jackal 机器人上，请问可以吗？ 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

Closed 2023-10-07.

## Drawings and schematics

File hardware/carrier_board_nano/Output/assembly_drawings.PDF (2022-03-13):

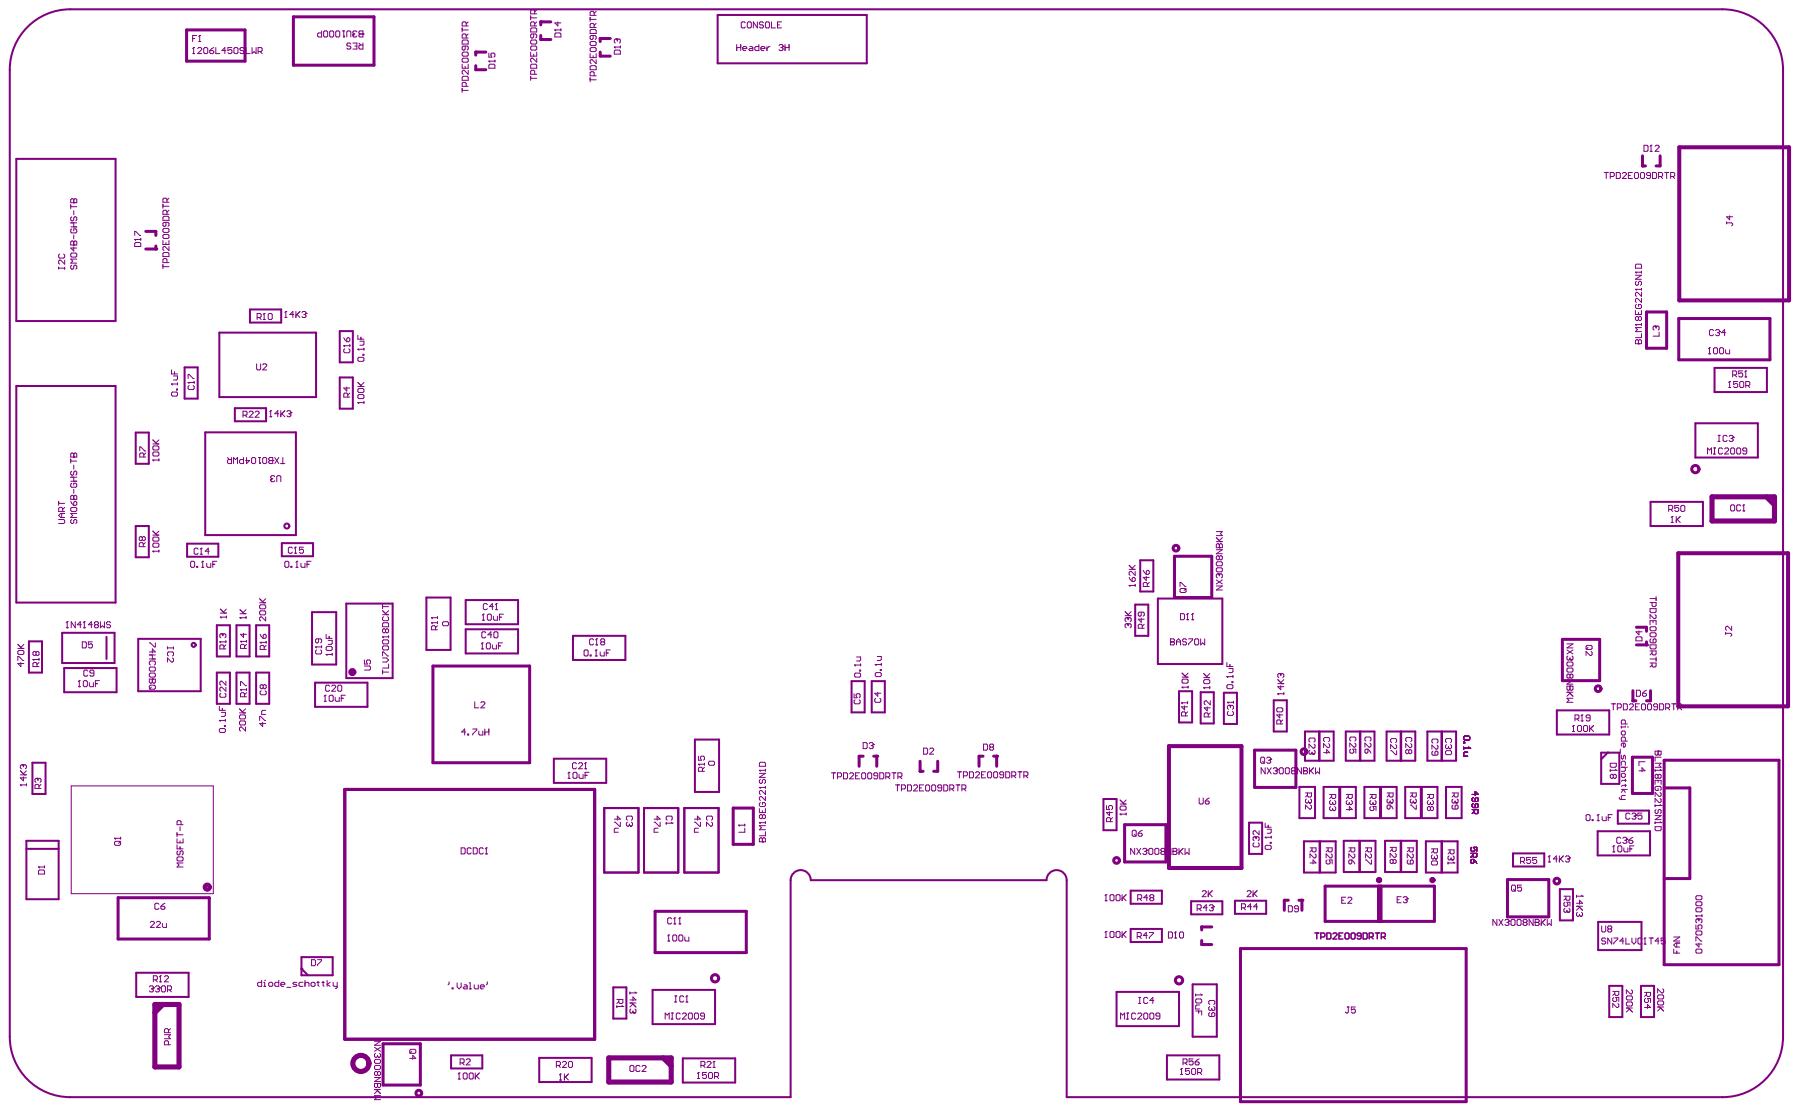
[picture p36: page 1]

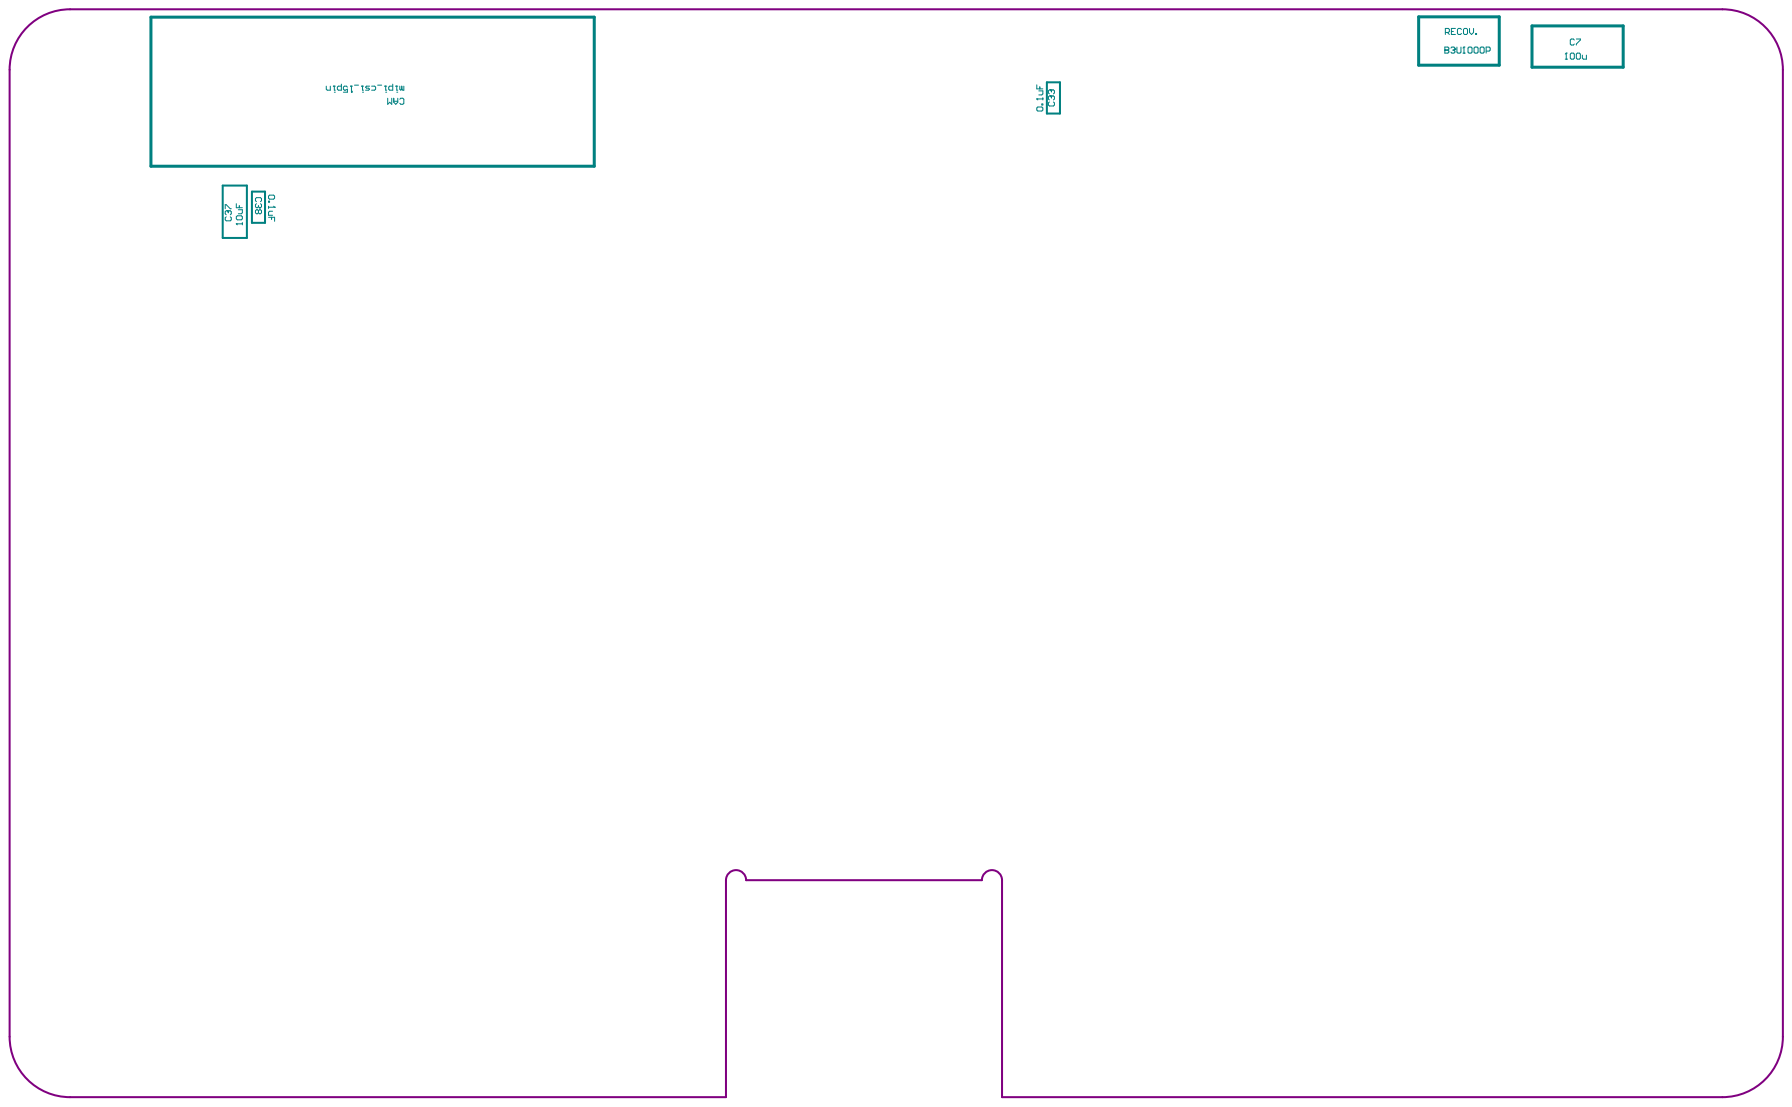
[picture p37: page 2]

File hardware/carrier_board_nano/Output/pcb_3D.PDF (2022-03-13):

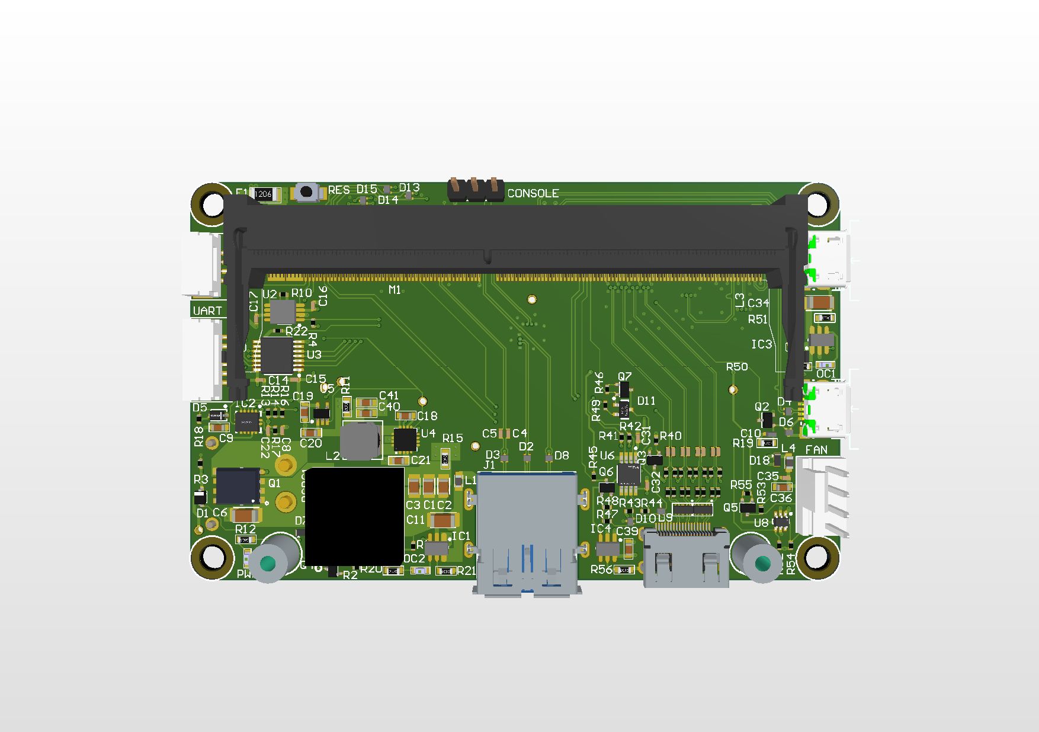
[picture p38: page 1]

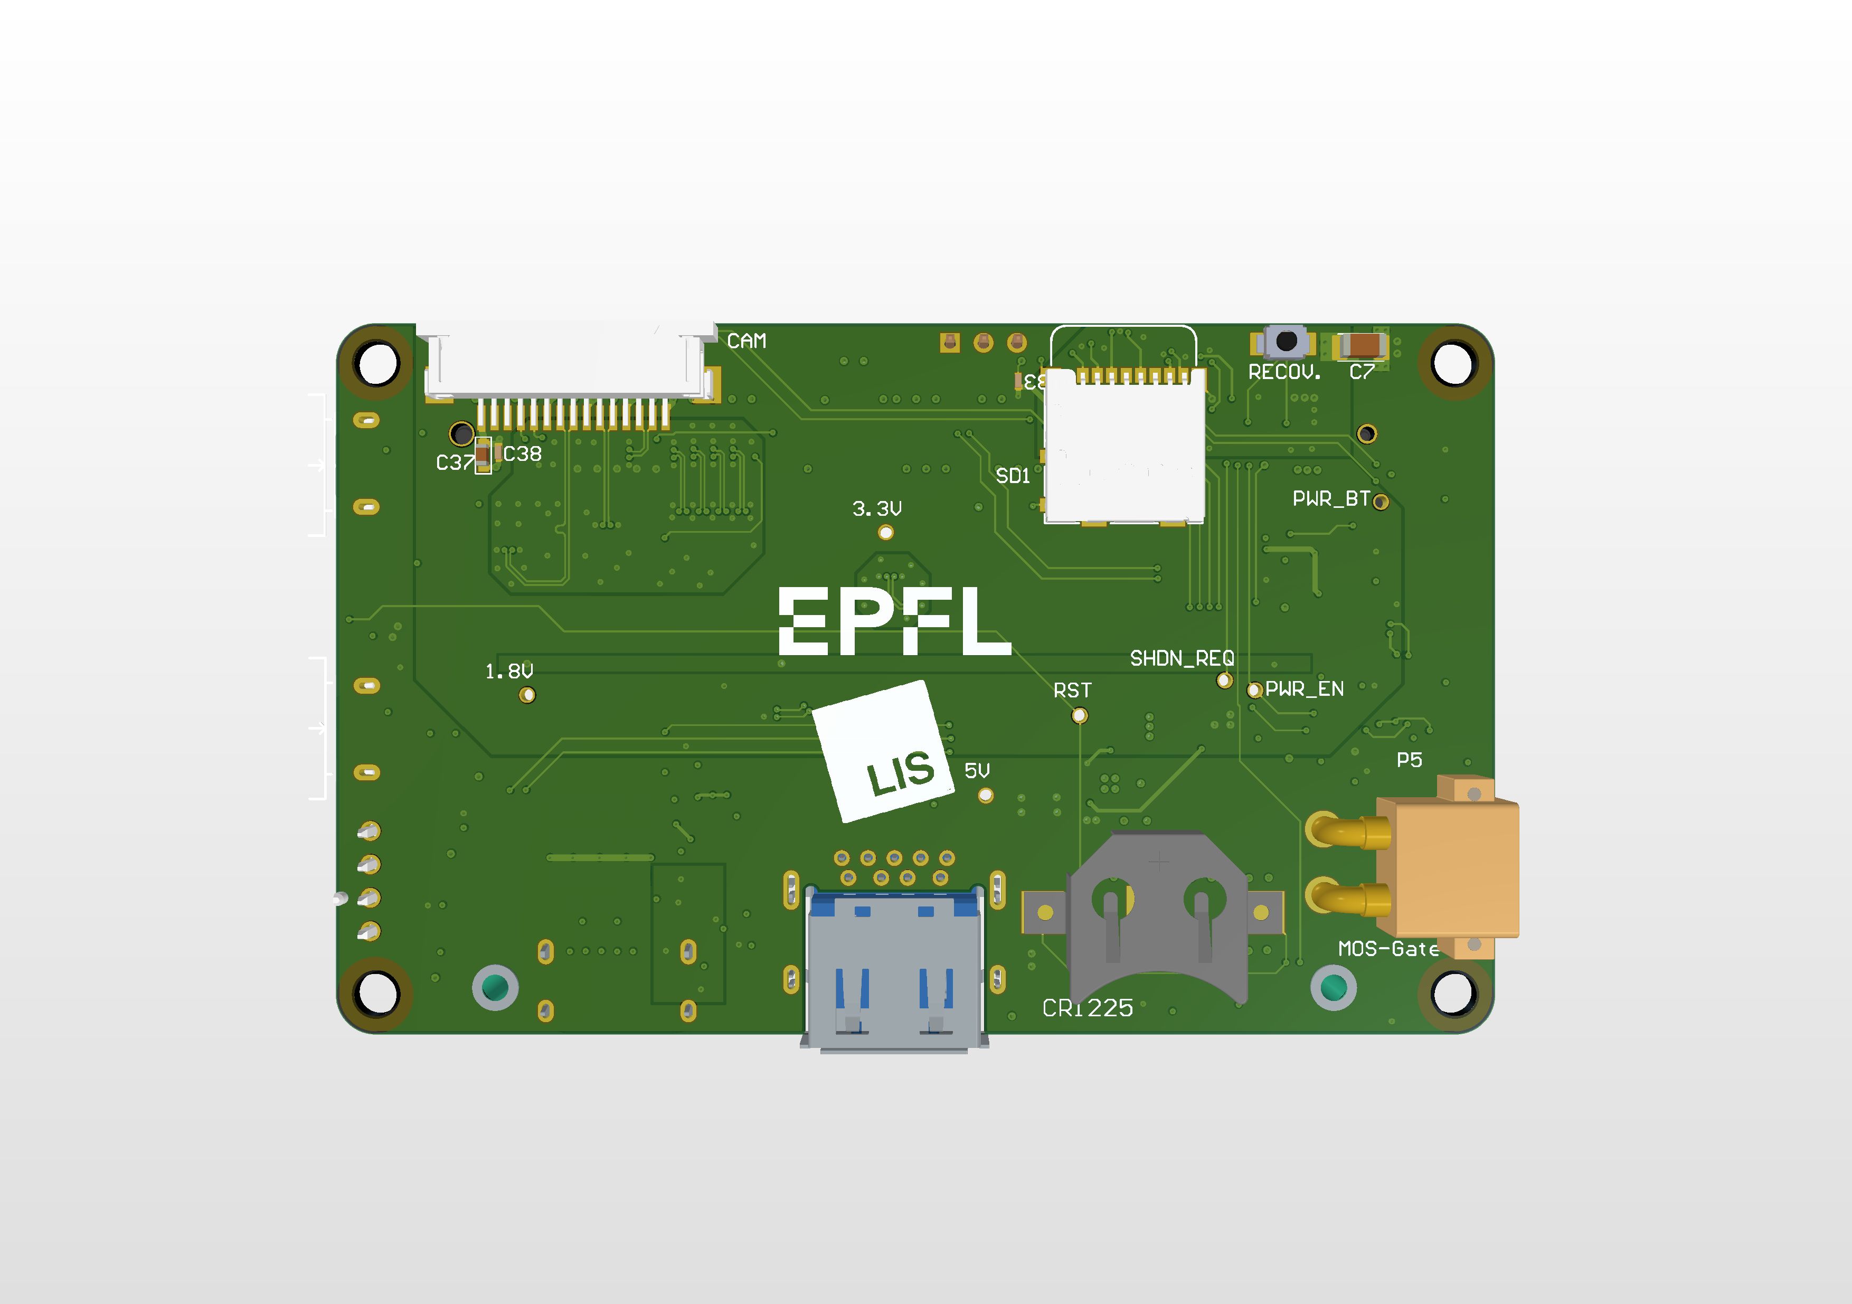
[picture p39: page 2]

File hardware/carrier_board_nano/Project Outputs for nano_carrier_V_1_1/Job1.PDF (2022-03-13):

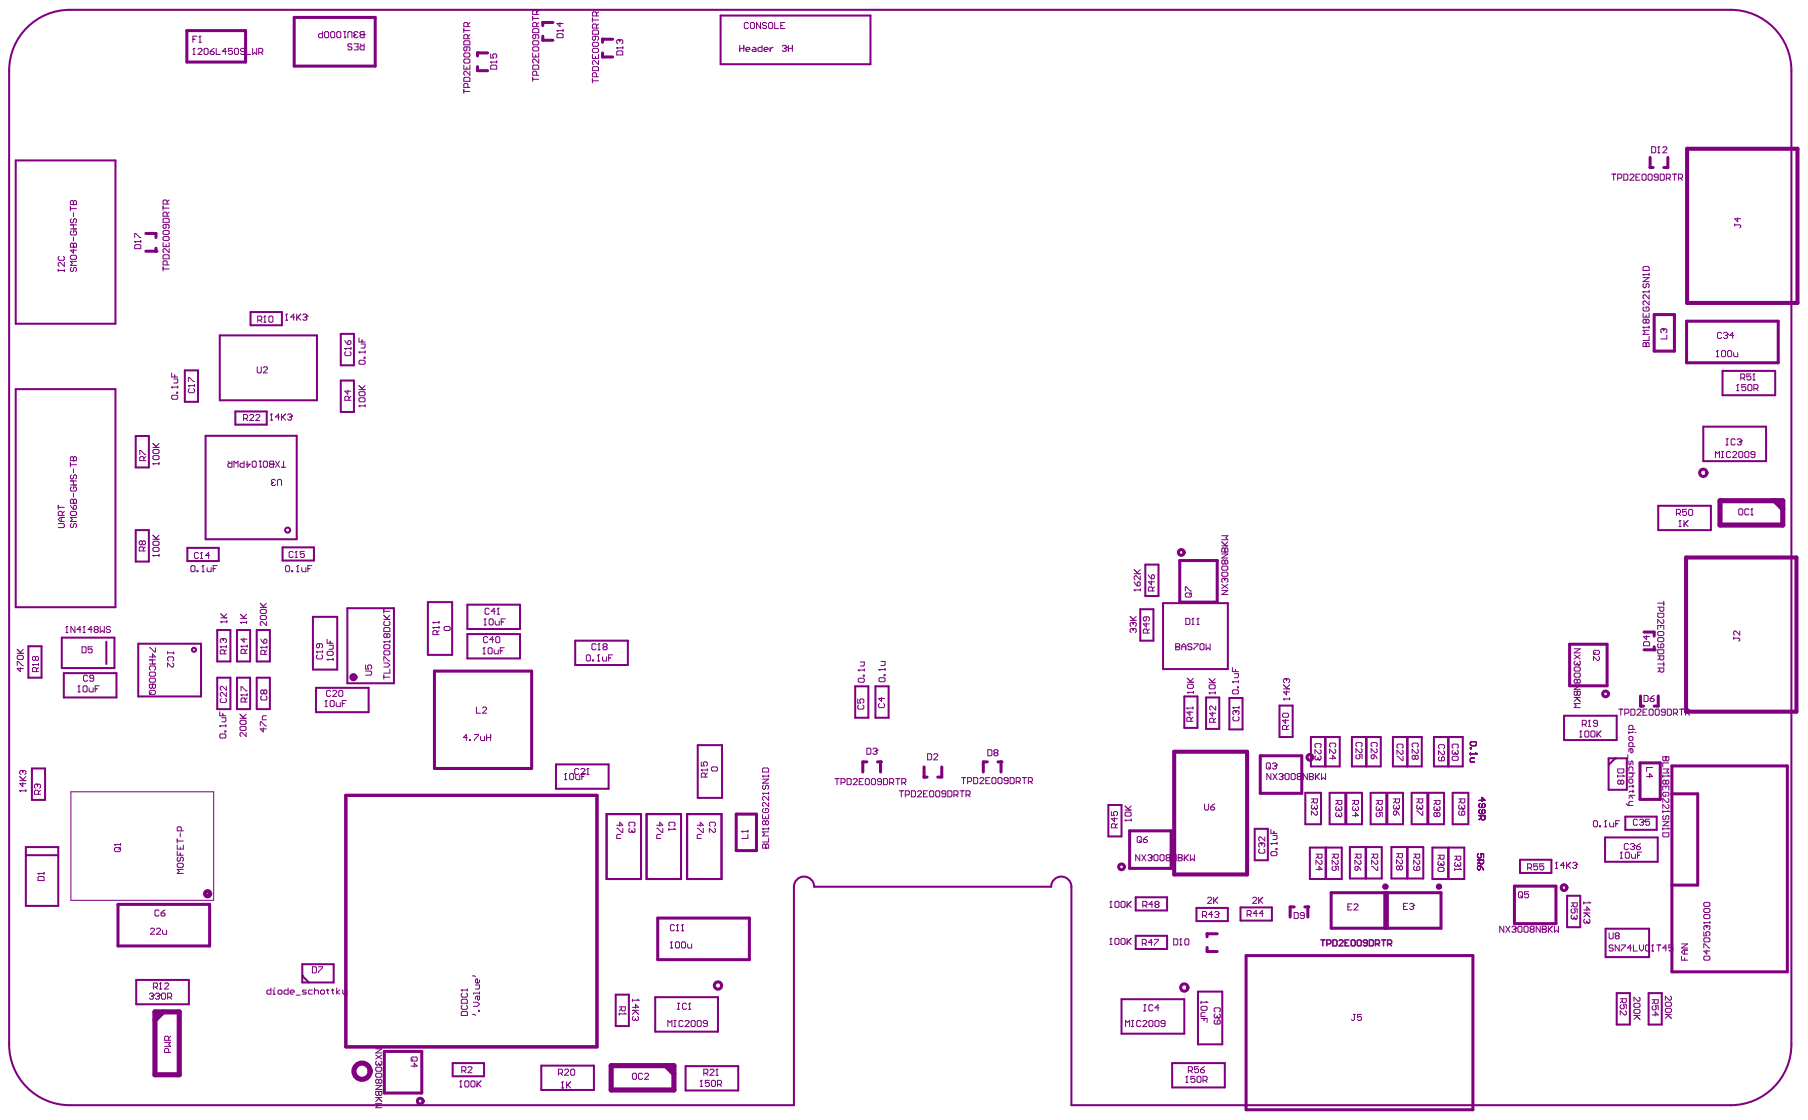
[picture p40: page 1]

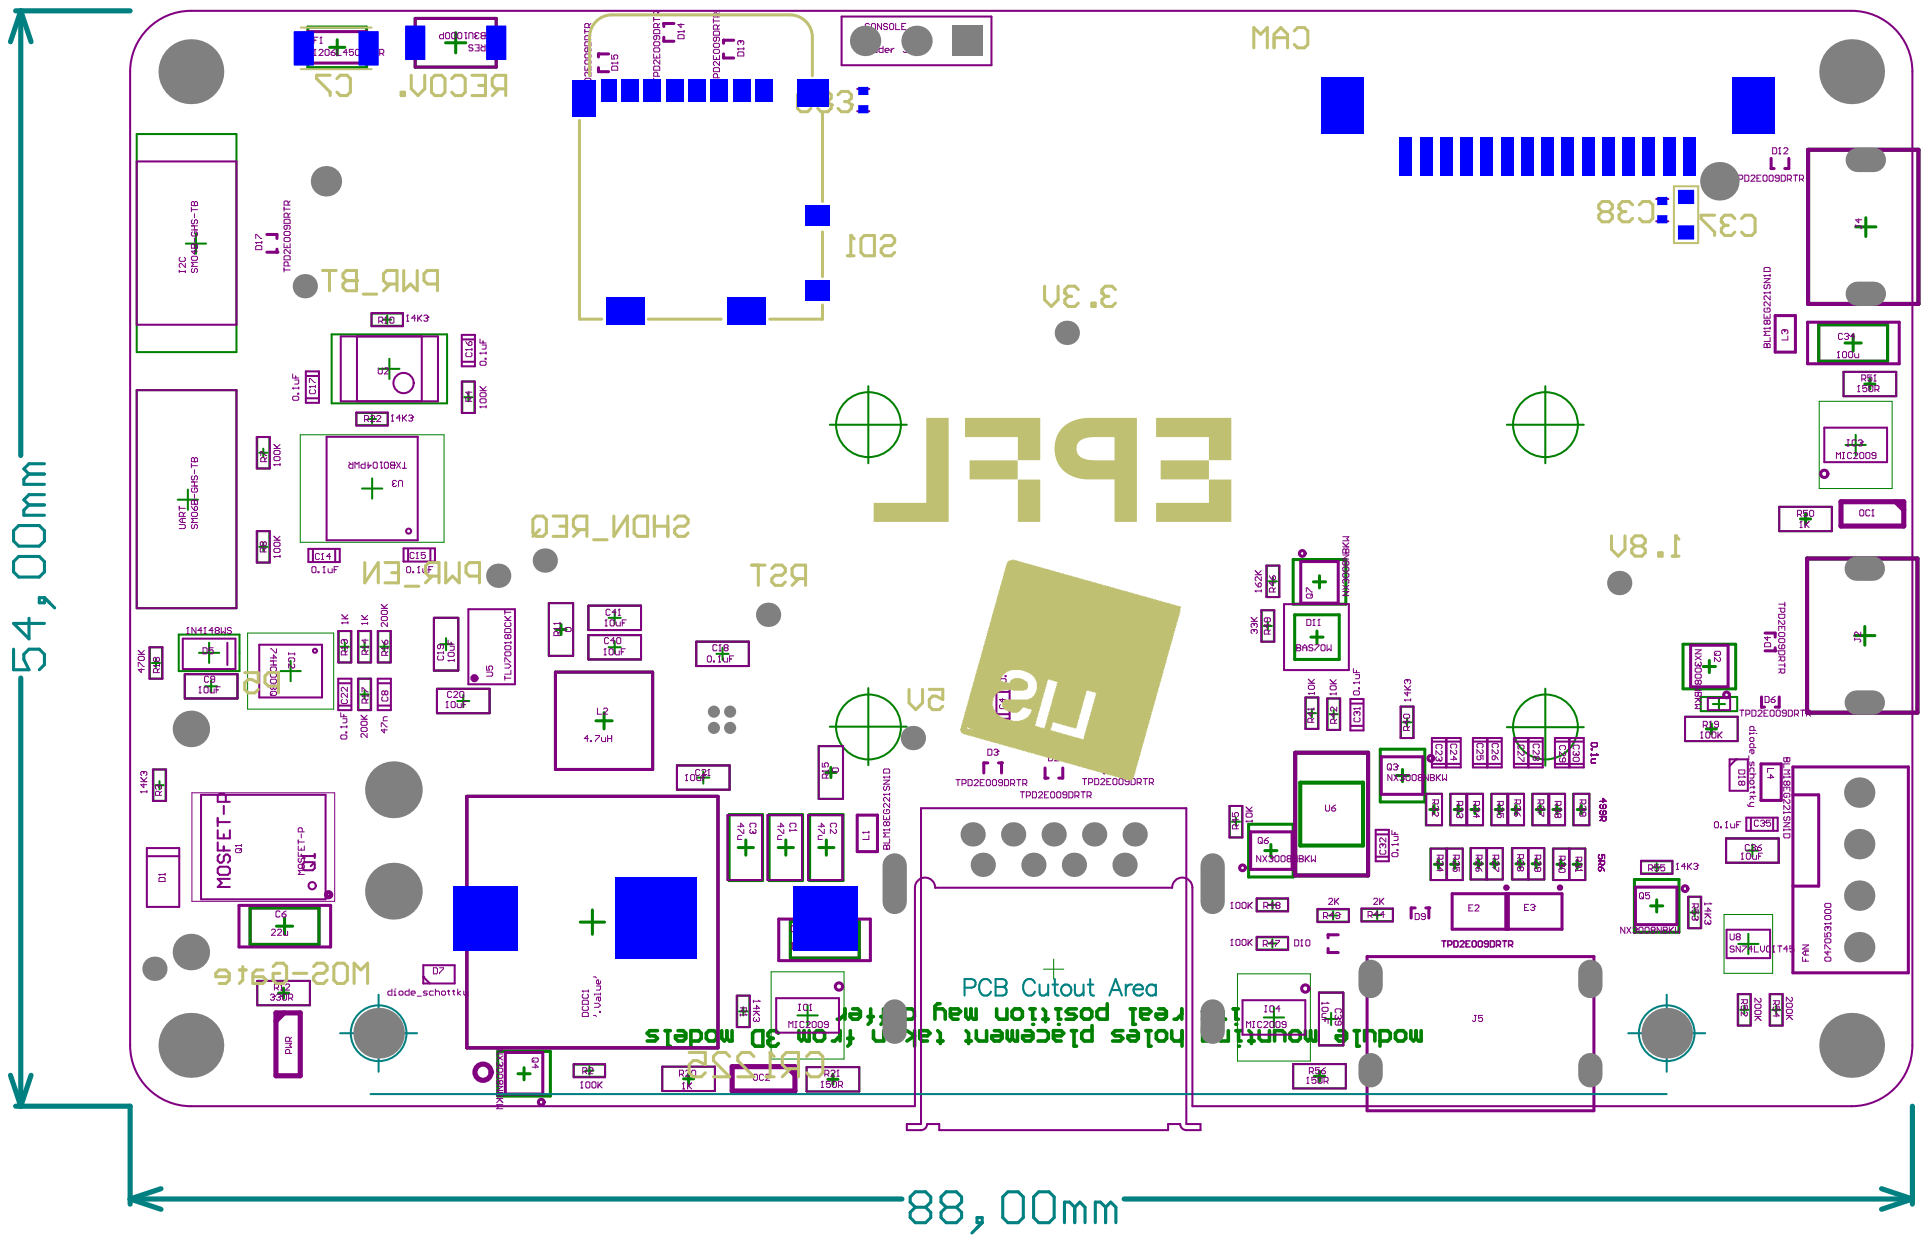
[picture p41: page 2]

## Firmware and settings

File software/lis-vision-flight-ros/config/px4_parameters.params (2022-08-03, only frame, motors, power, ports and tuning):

1	1	BAT_ADC_CHANNEL	-1	6
1	1	BAT_A_PER_V	36.367515563964843750	9
1	1	BAT_CAPACITY	-1.000000000000000000	9
1	1	BAT_CNT_V_CURR	0.000805664050858468	9
1	1	BAT_CNT_V_VOLT	0.000805664050858468	9
1	1	BAT_CRIT_THR	0.070000000298023224	9
1	1	BAT_EMERGEN_THR	0.050000000745058060	9
1	1	BAT_LOW_THR	0.150000005960464478	9
1	1	BAT_N_CELLS	3	6
1	1	BAT_R_INTERNAL	-1.000000000000000000	9
1	1	BAT_SOURCE	0	6
1	1	BAT_V_CHARGED	4.050000190734863281	9
1	1	BAT_V_DIV	18.100000381469726563	9
1	1	BAT_V_EMPTY	3.500000000000000000	9
1	1	BAT_V_LOAD_DROP	0.300000011920928955	9
1	1	BAT_V_OFFS_CURR	0.000000000000000000	9
1	1	MOT_ORDERING	0	6
1	1	MOT_SLEW_MAX	0.000000000000000000	9
1	1	PWM_MAIN_DIS1	-1	6
1	1	PWM_MAIN_DIS2	-1	6
1	1	PWM_MAIN_DIS3	-1	6
1	1	PWM_MAIN_DIS4	-1	6
1	1	PWM_MAIN_DIS5	-1	6
1	1	PWM_MAIN_DIS6	-1	6
1	1	PWM_MAIN_DIS7	-1	6
1	1	PWM_MAIN_DIS8	-1	6
1	1	PWM_MAIN_FAIL1	-1	6
1	1	PWM_MAIN_FAIL2	-1	6
1	1	PWM_MAIN_FAIL3	-1	6
1	1	PWM_MAIN_FAIL4	-1	6
1	1	PWM_MAIN_FAIL5	-1	6
1	1	PWM_MAIN_FAIL6	-1	6
1	1	PWM_MAIN_FAIL7	-1	6
1	1	PWM_MAIN_FAIL8	-1	6
1	1	PWM_MAIN_MAX1	-1	6
1	1	PWM_MAIN_MAX2	-1	6
1	1	PWM_MAIN_MAX3	-1	6
1	1	PWM_MAIN_MAX4	-1	6
1	1	PWM_MAIN_MAX5	-1	6
1	1	PWM_MAIN_MAX6	-1	6
1	1	PWM_MAIN_MAX7	-1	6
1	1	PWM_MAIN_MAX8	-1	6
1	1	PWM_MAIN_MIN1	-1	6
1	1	PWM_MAIN_MIN2	-1	6
1	1	PWM_MAIN_MIN3	-1	6
1	1	PWM_MAIN_MIN4	-1	6
1	1	PWM_MAIN_MIN5	-1	6
1	1	PWM_MAIN_MIN6	-1	6
1	1	PWM_MAIN_MIN7	-1	6
1	1	PWM_MAIN_MIN8	-1	6
1	1	PWM_MAIN_REV1	1	6
1	1	PWM_MAIN_REV2	1	6
1	1	PWM_MAIN_REV3	1	6
1	1	PWM_MAIN_REV4	0	6
1	1	PWM_MAIN_REV5	0	6
1	1	PWM_MAIN_REV6	0	6
1	1	PWM_MAIN_REV7	0	6
1	1	PWM_MAIN_REV8	0	6
1	1	PWM_MAIN_TRIM1	0.000000000000000000	9
1	1	PWM_MAIN_TRIM2	0.000000000000000000	9
1	1	PWM_MAIN_TRIM3	0.000000000000000000	9
1	1	PWM_MAIN_TRIM4	0.000000000000000000	9
1	1	PWM_MAIN_TRIM5	0.000000000000000000	9
1	1	PWM_MAIN_TRIM6	0.000000000000000000	9
1	1	PWM_MAIN_TRIM7	0.000000000000000000	9
1	1	PWM_MAIN_TRIM8	0.000000000000000000	9
1	1	SYS_AUTOSTART	2105	6

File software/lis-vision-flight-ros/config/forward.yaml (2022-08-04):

acquisition_frame_rate: 10.0
line_source: ExposureActive
auto_exposure_time_upper_limit: 30000
exposure_auto: 'Off'
exposure_time: 2000.0
auto_gain: 'Off'
gain: 0.0

# full sensor
image_format_roi_width:         1440
image_format_roi_height:        1080
image_format_x_binning:         1
image_format_y_binning:         1
image_format_x_offset:          0
image_format_y_offset:          0

# external trigger
acquisition_frame_rate_enable: false  # Frame rate halved without this setting!
enable_trigger: 'On'
trigger_selector: FrameStart
trigger_source: Line3

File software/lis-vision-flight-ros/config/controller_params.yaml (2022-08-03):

target:
  longitude: 6.568811145944444
  latitude: 46.52594051405556
  altitude: 486.3

thrust: 0.35
distance_tag_target_z: 0.75
pitch_offset: -2.8
time_without_detection: 0.5
publish_rate: 50.0

gravity_constant: 9.806650162
camera_pose:
  t_body_cam_body: [0.3, 0, -0.06]
  R_body_cam: [0, 0, 1, -1, 0, 0, 0, -1, 0] # row wise 3x3 rotation matrix

syncing:
  queue_time_range: 1.0 # duration in secs determining the queue lengths
  imu_freq: 100 # frequency of IMU message
  vel_freq: 50 # frequency of velocity_local message
  cam_freq: 50 # frequency of camera images
  gps_freq: 10 # frequency of GPS measurements

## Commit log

2022-03-13 hardware update
    [Bill of Materials-nano_carrier_V_1_1.xlsx, Bill of Materials-nano_carrier_V_1_1_old.xlsx, Bill of Materials-nano_carrier_V_1_1_tmp.xlsx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]
2022-03-14 readme update
    [gnss_antenna_holder.SLDPRT, gnss_antenna_holder.STEP, gnss_antenna_holder.STL]
2022-04-13 carrier hardware update
    [Bill of Materials-nano_carrier_V_1_1.xlsx, Bill of Materials-nano_carrier_V_1_1_old.xlsx, Bill of Materials-nano_carrier_V_1_1_tmp.xlsx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]
2022-08-03 vision_control files added, whycon submodule added
    [controller_params.yaml]
2022-08-03 updating readme and params
    [px4_parameters.params]
2022-08-03 README update, wiring, software
2022-09-06 update GNSS antenna STL link
